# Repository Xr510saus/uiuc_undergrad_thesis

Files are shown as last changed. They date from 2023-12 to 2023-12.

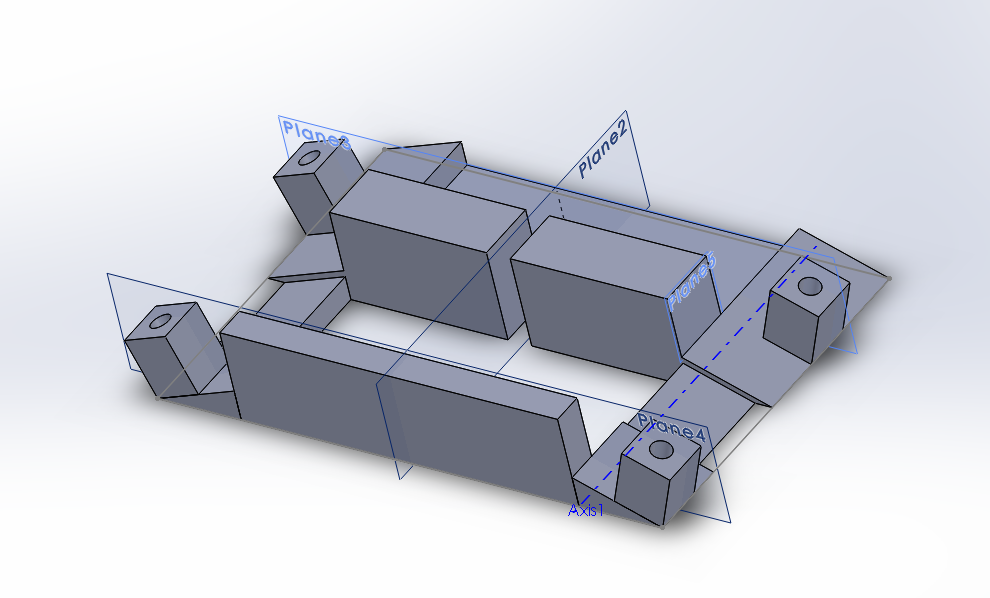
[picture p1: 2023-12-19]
images/chassis 2.png

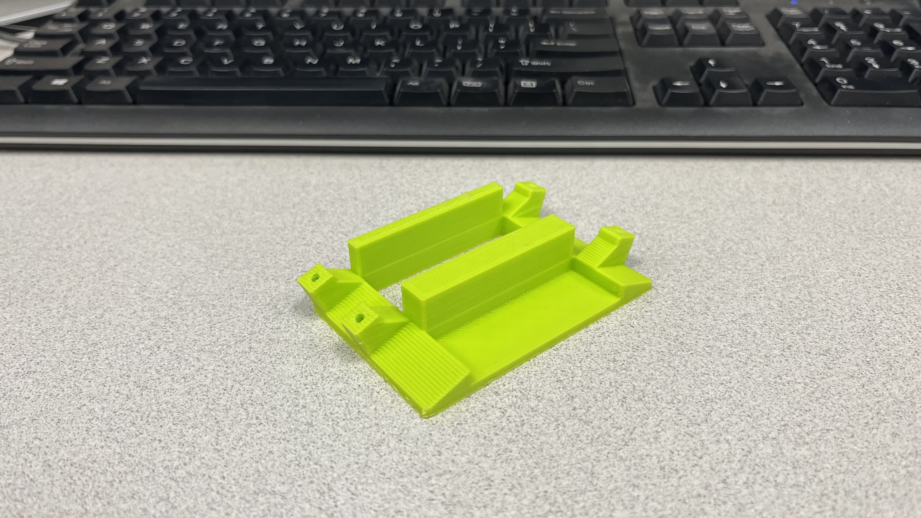
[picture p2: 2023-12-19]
images/first chassis part 2.jpg

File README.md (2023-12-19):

# uiuc_undergrad_thesis

## Project description

For my undergraduate (UIUC) thesis, I designed a cable-driven soft robot to crawl on 2D surfaces. This repo contains the entire history of the project, which lasted over my final two semesters at UIUC, starting from my funding application, through my progress reports, and finally ending at the FINAL DELIVERABLES directory, which contains my actual thesis and the slides I presented at the Undergraduate Thesis Symposium.

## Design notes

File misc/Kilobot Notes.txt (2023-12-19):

Purpose of swarm robotics:
* Validate collective control algorithms irl, not just through simulation

What other groups have done:
* Tested out on 10s, 100s of robots
* Limited by robot cost and operational complexity
	* Turning robots on/off, charging, controlling, and programming

Main point:
* All operations of the robot must work on the collective as a whole and be scalable

Kilobot:
* $14 worth of parts
* 5 min assembly
* Features
	* Differential drive locomotion
	* On-board computation power
	* Neighbor-to-neighbor communication
	* Neighbor-to-neighbor distance sensing

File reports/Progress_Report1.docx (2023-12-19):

Stephen Zhu

Srzhu3

ECE 496

In the past few weeks, I created some actuators to determine what parameters I would be interested in testing. It was my first time making CAD files to create molds, so it took some time to model the actual actuators before creating the molds and printing them using our 3D printer. I made 4 different molds, switching between the height of the actuator (15mm and 30mm) and the canal width, defined as the width between the valley and the bottom of the actuator (2.5mm and 7.5mm). Another mold was made with actuator height 25mm and canal width 5mm, but with double the width of the actual actuator. Included are two images, the first one shows one side of the mold for the 15mm 2.5mm actuator, while the second shows one side of the mold for the 30mm 7.5mm actuator. From the images, the canal width can be seen as the distance from the top of the molds to the peaks of the triangles

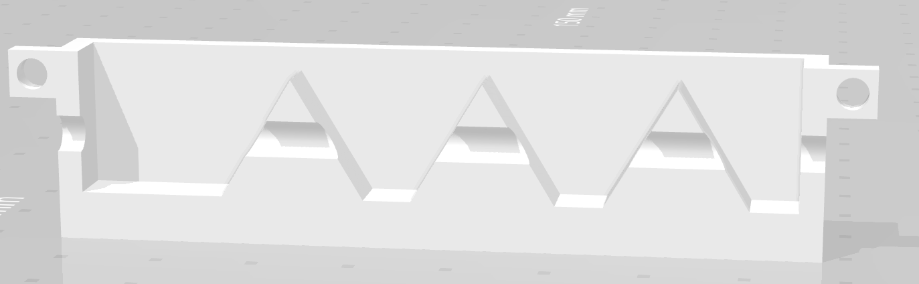
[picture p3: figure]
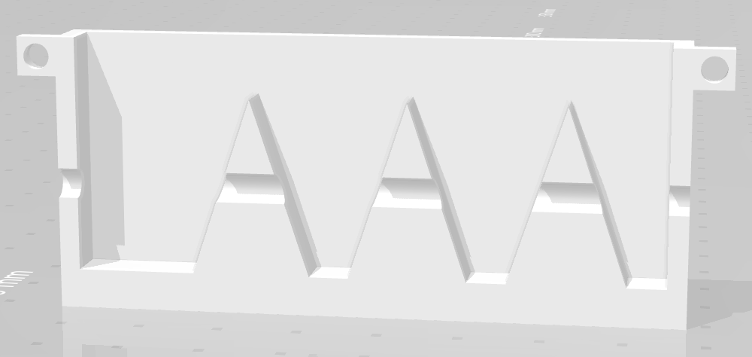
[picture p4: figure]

The molds were made such that each mold has two halves that can be connected by screws on both ends. In the middle, a cylindrical cavity is made, so that before each half is pushed together, a piece of tubing can be put inside the cavity. Silicon rubber is then poured into the mold and allowed to harden.

To further process each actuator, when the actuators are taken out, additional bits of rubber are trimmed off, and the parts of the tubing that aren’t within the actual actuator are cut off. Below are the two actuators made from the above molds

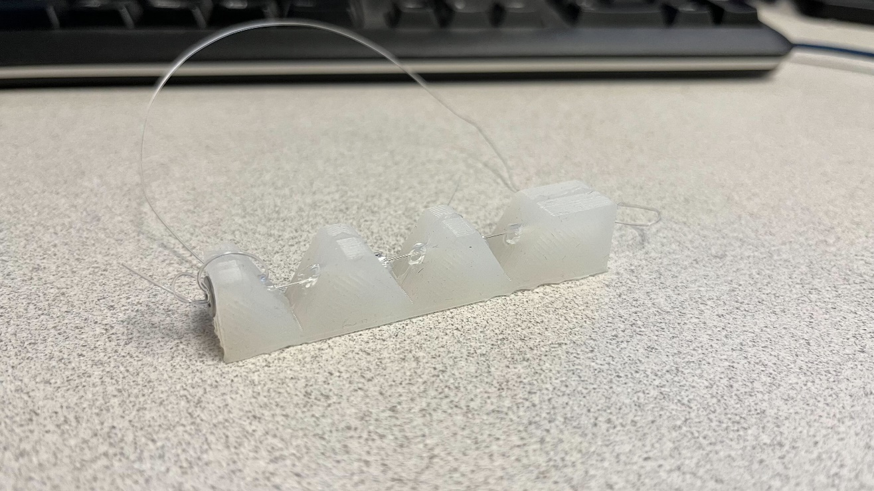
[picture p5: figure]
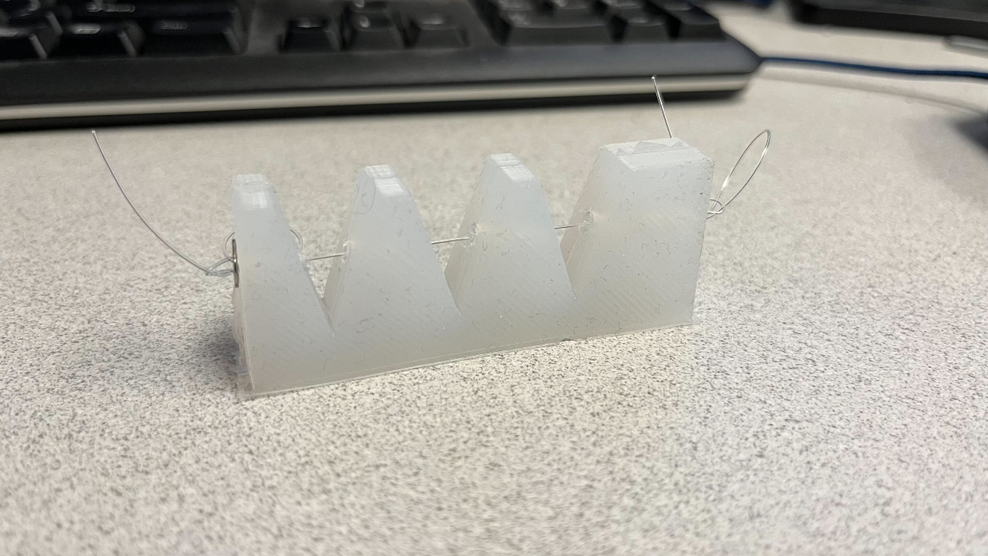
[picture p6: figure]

A total of 10 actuators were made, using two different materials (Ecoflex 50 and Dragon Skin 30) and each of the 5 molds. I then tried testing different aspects for each of the actuators and comparing them. Ultimately, the Ecoflex actuators were too soft to have any significant effect, and it only took at most 150 grams of weights to bend them fully. The Dragon Skin actuators were stiffer, and ranged from 110 g to 800 g of weight to bend fully. Below is a picture of the data taken, as well as a verbal description of the testing procedure to determine the weights needed to bend.

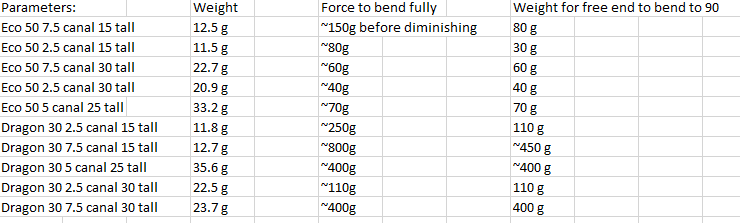
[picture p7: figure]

Testing Procedure:

1. Set actuator against side of table with vertical drop (ensure string doesn’t touch edge of table to factor out table friction
2. Add weights on to the hook weight and drop it onto the loop at the end of the actuator
3. Compare bend with bend through finger pulling
4. Change weights and redrop onto the line to ensure there isn’t any retention of shape from the actuator that affects the reading
5. Record amount of weight that is close enough to the full finger bend distance before significant diminishing marginal bend

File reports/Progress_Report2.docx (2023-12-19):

Stephen Zhu

Srzhu3

ECE 496

In order to test out the previously made actuators, I had to design a prototype body for the robot to attach the actuators to. Below is an image of the first design I made in SolidWorks. These designs were 3D printed, as we have not yet finalized the design for the robot itself, and 3D printing is significantly quicker and easier to make prototypes with.

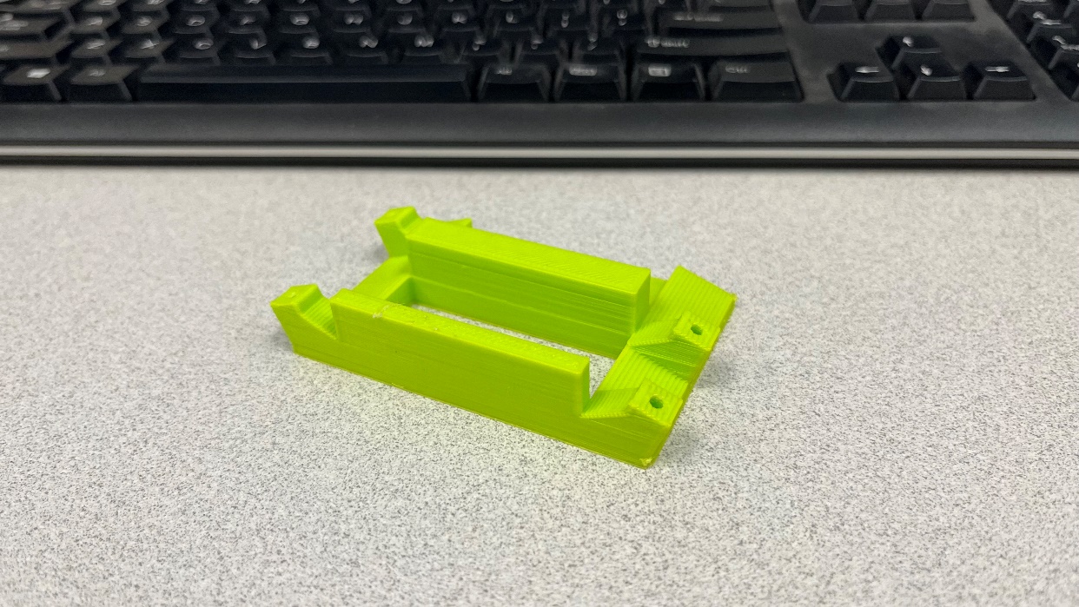
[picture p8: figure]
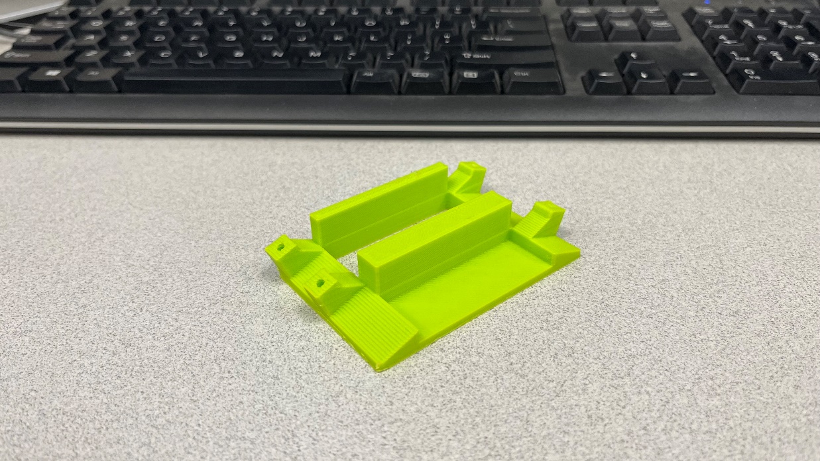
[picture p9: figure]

A few problems came with this design. First, the underside of the back half of the robot was too thick, so it added on a lot of time to the print. Second, I wanted to place a servo in the center to actuate the actuators on both sides, but my design failed to account for the fact that one end of the motor had cables exiting it, so the servo couldn’t fit inside the space I allotted it. Lastly, I designed the body in such a way that I could test the 15mm tall actuators on the “left” side and the 30mm tall actuators on the “right” side. This limited me from testing 30mm actuators on both sides, but since I had only 1 of each actuator, and I wanted to test the actuators first, this wasn’t a huge issue.

With the actual tests of the actuators, I quickly realized a trend. In the previous report, I included a table of how much weight it took to bend the actuators and one column detailed the weight needed to fully bend the actuator. Any actuator that had less than 400g as its entry wasn’t able to move the printed body at all. In other words, the Ecoflex 50 actuators were all too soft to have any noticeable effect on movement, and only a select few actuators were actually stiff enough to cause movement. It should be noted that the slopes that the actuators are attached on are at 20 degrees above the horizontal. When the actuators that were actually able to move the body were attached, some of them were stiff enough to raise the body above the ground.

The circuit to move the body was made using an ItsyBitsy 3V development board, attached to a computer though a USB micro cable. The reason it was attached to a computer was to ensure the voltage and current were high enough to run the servo. The program to actually move the servo was made on the Arduino IDE, as the ItsyBitsy board is capable of supporting Arduino IDE. Below is a picture of the circuit on a breadboard.

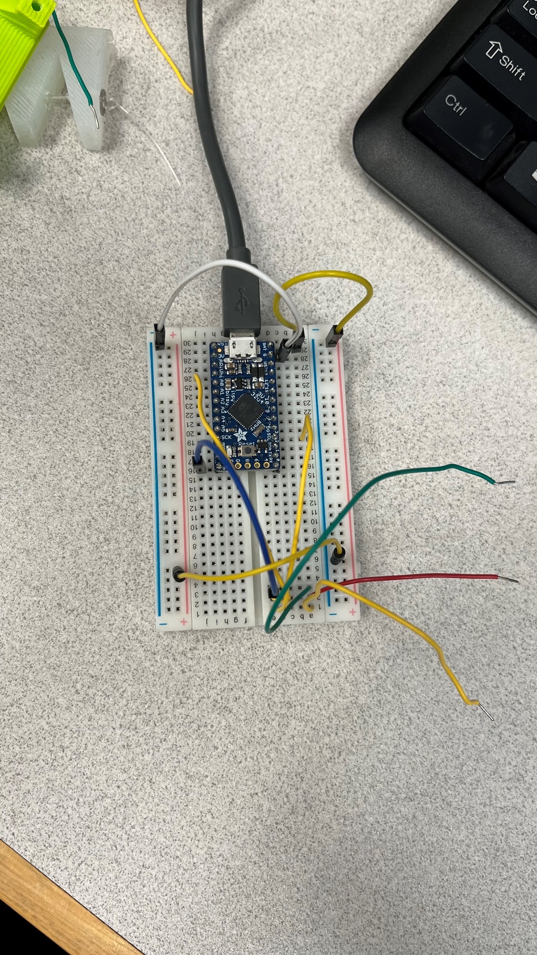
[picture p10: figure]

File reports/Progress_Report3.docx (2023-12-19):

Stephen Zhu

Srzhu3

ECE 496

To address the previous problems with the body, I redesigned it to allow space for the servo, reduce the print time, an allow the same actuator to be put on both sides.

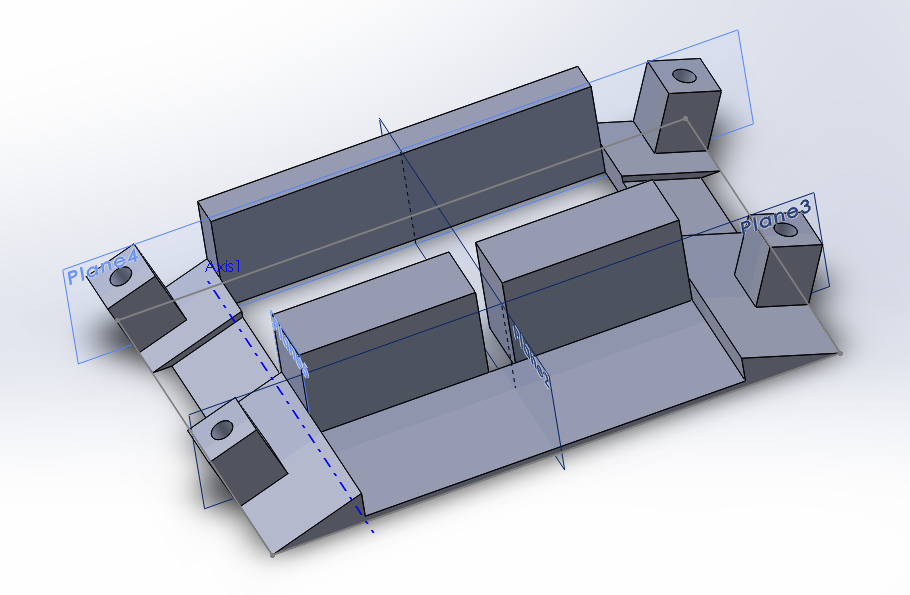
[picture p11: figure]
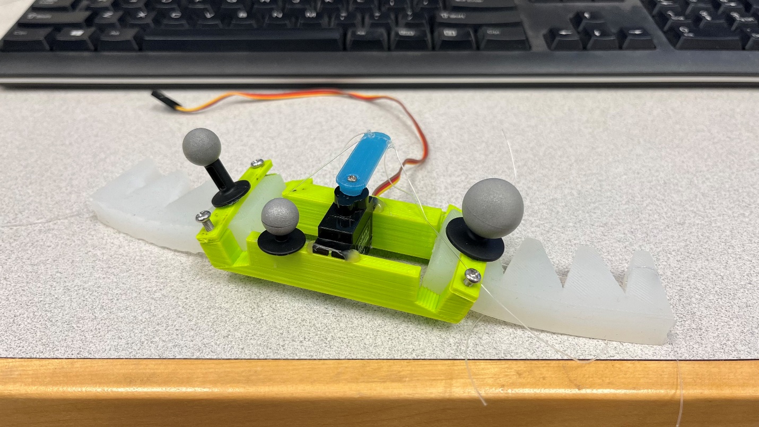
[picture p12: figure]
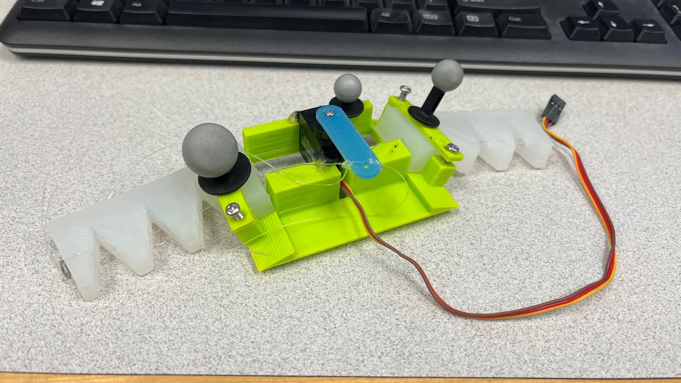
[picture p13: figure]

Additionally, grooves were introduced within the actuator attachment points to constrain the 15mm tall actuators so that they won’t wiggle around when put in. Additionally, the actuators that were able to move the body were duplicated (15 tall, 7.5 width canal and 30 tall, 7.5 width canal) and new actuators with 20 degree bends at the end were created.

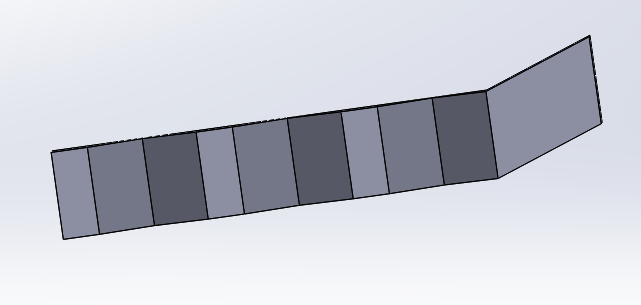
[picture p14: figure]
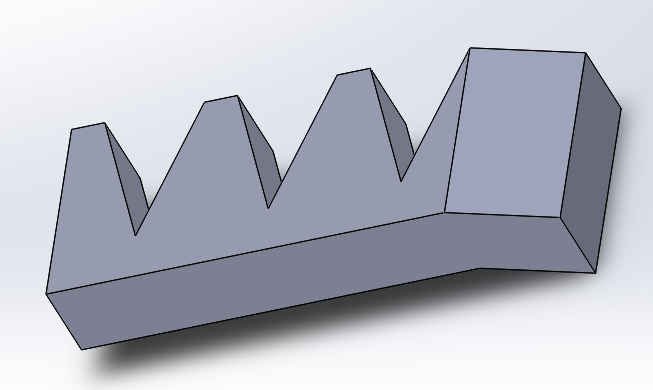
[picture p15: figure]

These actuators were made to account for the 20 degree slope that is on the body, and to bring more of the actuator to touch the ground. These were modified from the 30 tall, 7.5 width actuators. Each pair of the actuators were attached to the body and tested for speed (efficiency) though a motion capture system. Since the motion capture system is too far away for the cable to reach, the circuitry was modified to allow for 2 LiPo batteries in series to power the system. Below are graphs made using the data.

15 tall, 7.5 width; velocity: 0.8 mm/s

30 tall, 7.5 width; velocity: 2.1 mm/s

30 tall, 7.5 width, bent actuator; velocity: 0.3 mm/s

From the data, we can see that in terms of overall speed, the 30 tall, 7.5 width actuator performed the best. Additionally, I now believe that what caused the body of the robot to move is due to the edges of the actuators, not the bottom face, which explains why the bent actuators performed worse. It should be noted that the 15 tall, 7.5 actuator was so stiff that the body was completely off the ground, and when the actuators began moving, the robot tipped over slightly due to how unbalanced the system was.

In the future, I want to design some actuators with grooves at the bottom, and see if that can artificially create an “edge” for the actuators to move off of. Additionally, I want to experiment with making actuators with “legs bent in one direction,” which would allow the actuator to return smoothly to its default position, but give a lot of resistance when the actuator is being pulled.

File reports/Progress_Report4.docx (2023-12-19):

Stephen Zhu

Srzhu3

ECE 499

Progress Report 4

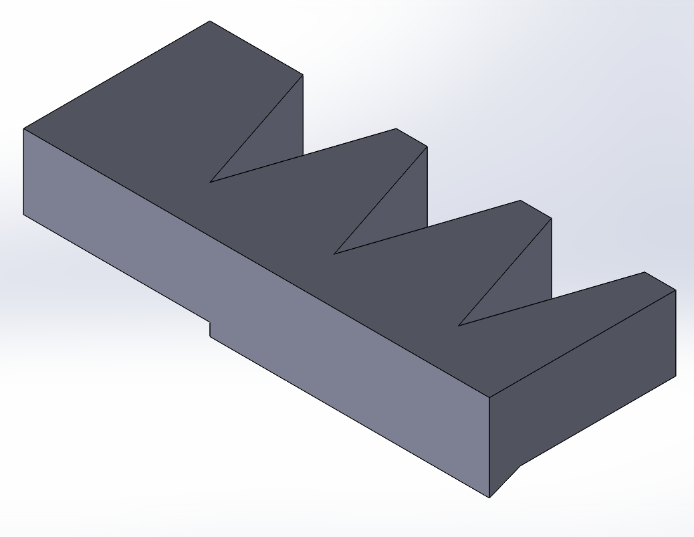
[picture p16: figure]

I continued to test out different actuator designs, expanding on the thought of introducing “legs” or other shapes on the bottom of the actuators. My main focus was on improving the “edge” of the actuator, since the net motion of the robot seemed to be driven by how well the edge was able to push off against the ground. As shown in the images below, I tried designs such as adding a more distinct “edge” to the actuator and three “legs” to the edge.

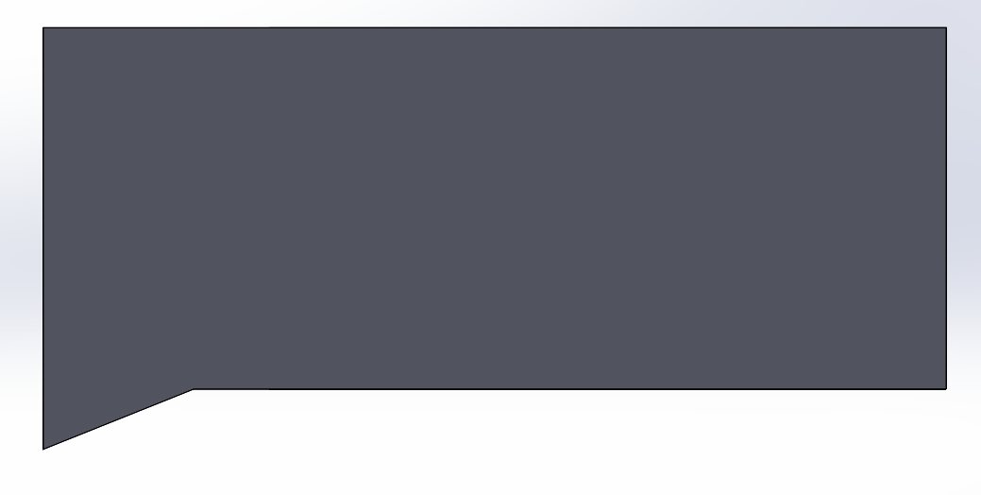
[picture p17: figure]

Single-edge isometric view Single-edge side view

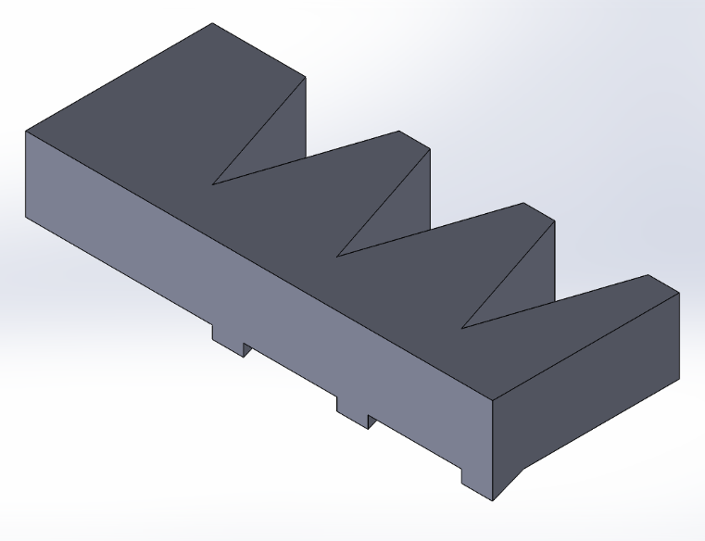
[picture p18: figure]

Tri-edge (tri-leg) isometric view

Additionally, I experimented with adding a tilt into the actuator, to see if that would enable better “grip” from the new edges, as well as reversing the direction of the legs to see if that would enable movement in the reverse direction.

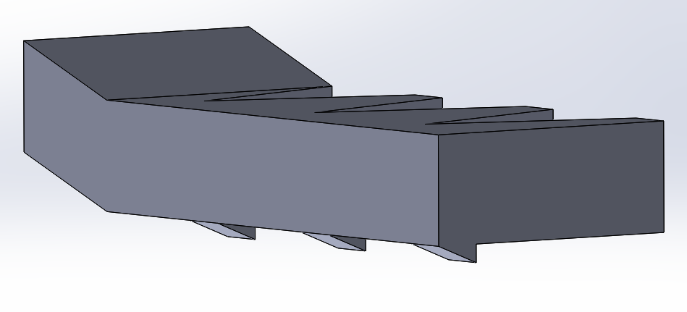
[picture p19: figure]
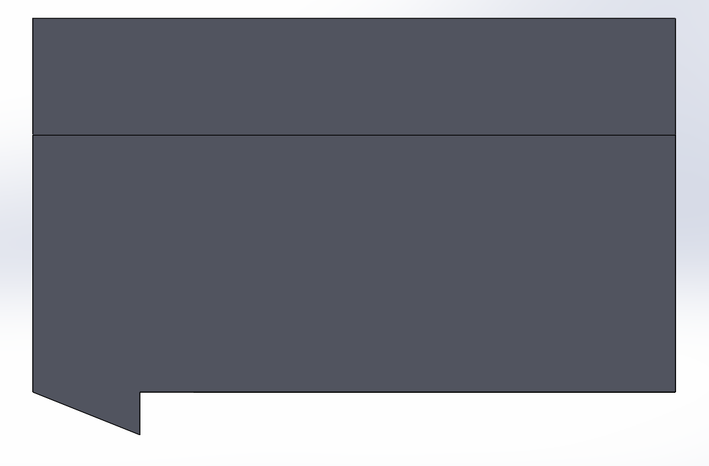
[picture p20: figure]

Tilted and reverse-leg isometric view Tilted and reverse-leg side view

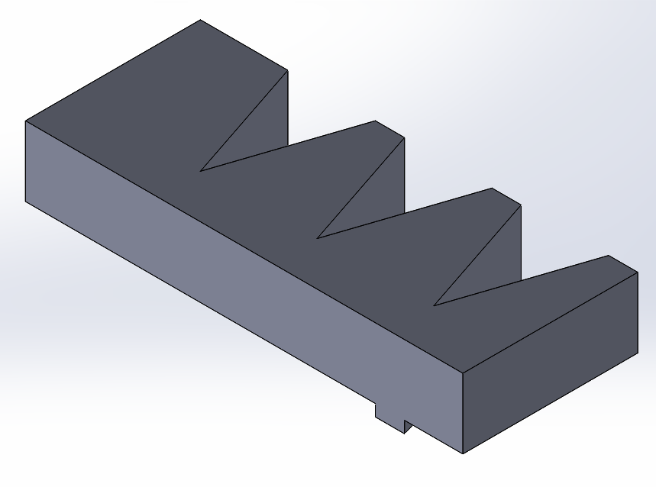
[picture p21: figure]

After using the motion capture system to test the efficiency of the actuators, it was clear that introducing a tilt to the actuator was detrimental to its efficiency, since there was less pressure pushing the edge of the actuator into the ground. Reversing the legs also did nothing. Between the single-edge and tri-edge designs, the tri-edge performed better. On further inspection through video footage, it seemed like when the actuators were being pulled, the smooth side of the legs would get pulled back normally. However, when the actuator was being released, the edges of the legs would catch the ground, causing them to greatly increase the friction and create a larger net motion than the other designs. I then tried to create a design with only one leg to further reduce the friction when the actuator was being pulled, but it proved to be less effective than the design with three legs.

Single-leg design

Lastly, I experimented with increasing the speed of the servos. As expected, the faster the servos went, the faster the robot would go through an entire movement cycle, and thus the faster the robot moved.

Below is the graph of the increased speed, tri-edge/leg design.

From the line of best fit, the velocity of the robot was around 9.1 mm/s.

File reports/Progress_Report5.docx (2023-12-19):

Stephen Zhu

Srzhu3

Progress Report 5

With the actuator design finalized, I turned to working on designing the circuitry on Eagle and making the soft prototype body.

For the circuitry, I used the Adafruit ItsyBitsy board and Arduino to control two servos, one for each actuator. The initial prototype relied on one servo to pull each actuator back and forth, but with the use of two servos, separate control of each actuator can be achieved. I then experimented with using a 3V-5V voltage booster, since the nominal voltage of the battery was on the low side for the servos. I eventually found that just directly linking the servos to the output of the booster without extra resistance was fine and didn’t damage the servos, and I finalized the circuit design, shown below. The rightmost component is the ItsyBitsy board, the top left is the battery-to-board connector, the middle left is the 3V-5V booster, and the bottom two are the servo-to-board connectors.

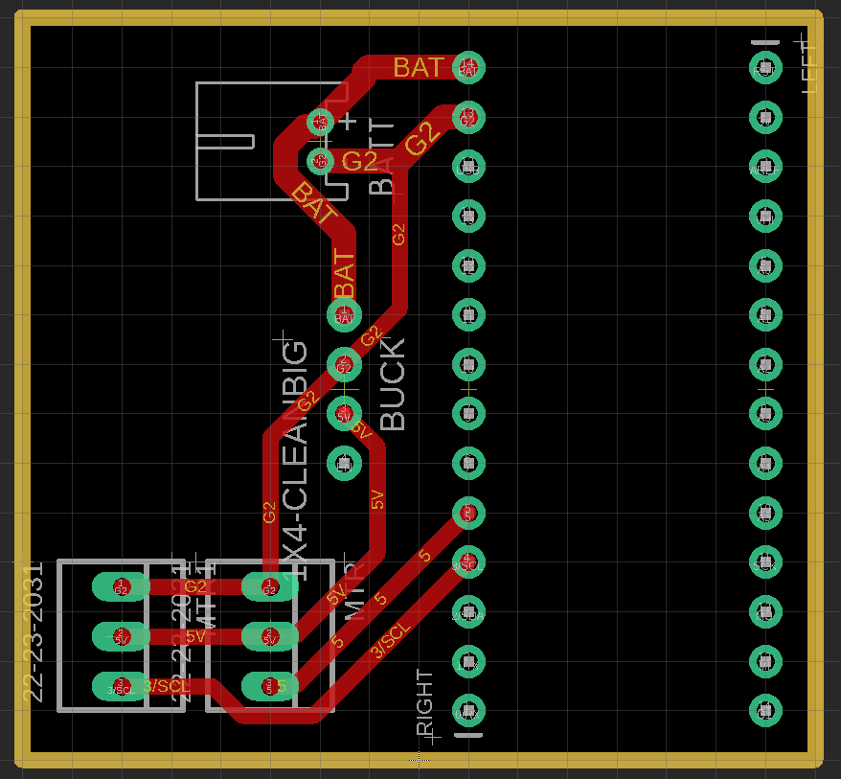
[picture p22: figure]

I then began to prototype a soft body, to verify if my prior experiments would work once I shifted away from the 3D-printed body. Initially, I tried making a mold based off of the previous design, but the screw clamps I used to hold the actuators in place wouldn’t work on a soft body. Also, the lack of material surrounding the servos proved to be detrimental, since the servos would turn in place rather than pull on the actuators’ cables.

To fix this, I surrounded the servos with material, and adjusted the actuator housing so that I would need to use more silicone rubber to glue the actuator to the body. Additional, I added a small compartment to hold the battery, and created a well to be able to glue the circuit board onto the body better. The design is shown below.

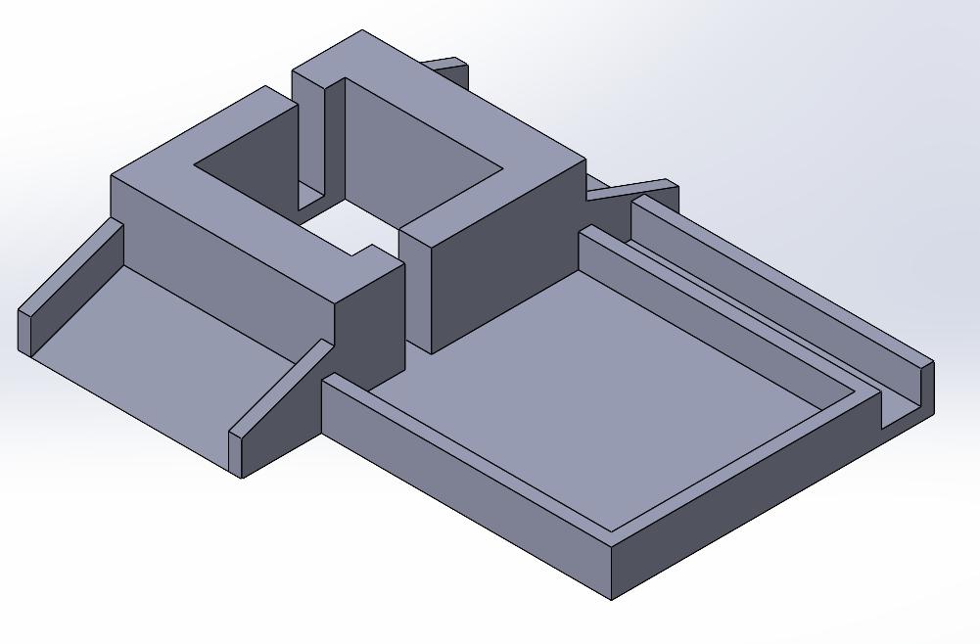
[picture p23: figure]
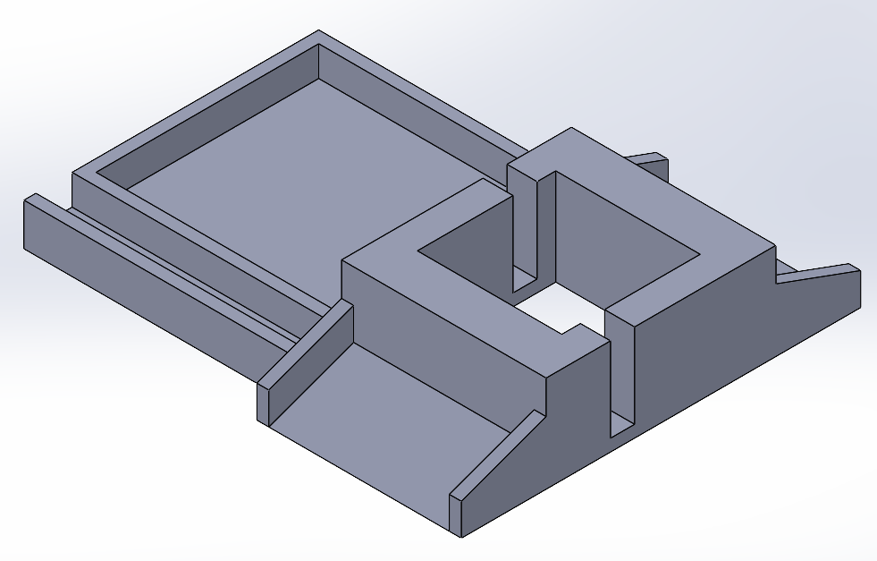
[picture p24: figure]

With these two elements, we were finally able to make the robot completely untethered and gather data on it using the motion capture system. The completed prototype is shown below, as well as the data.

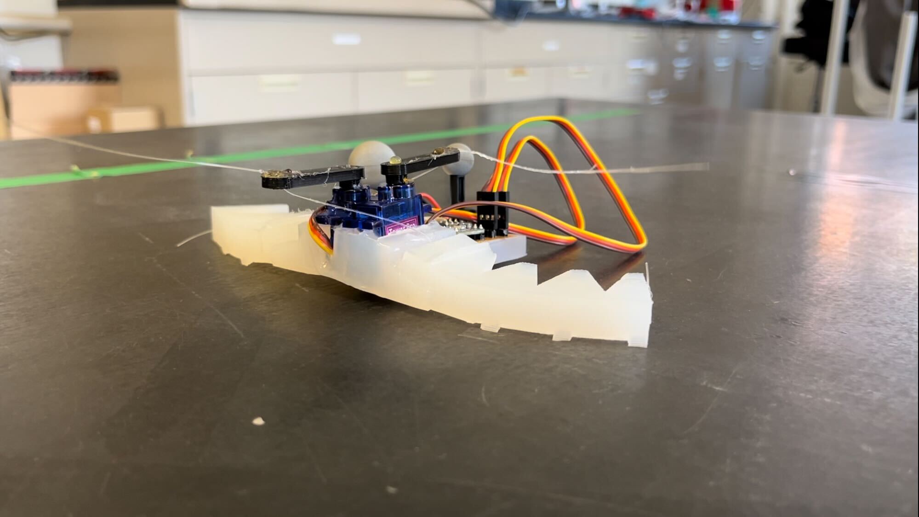
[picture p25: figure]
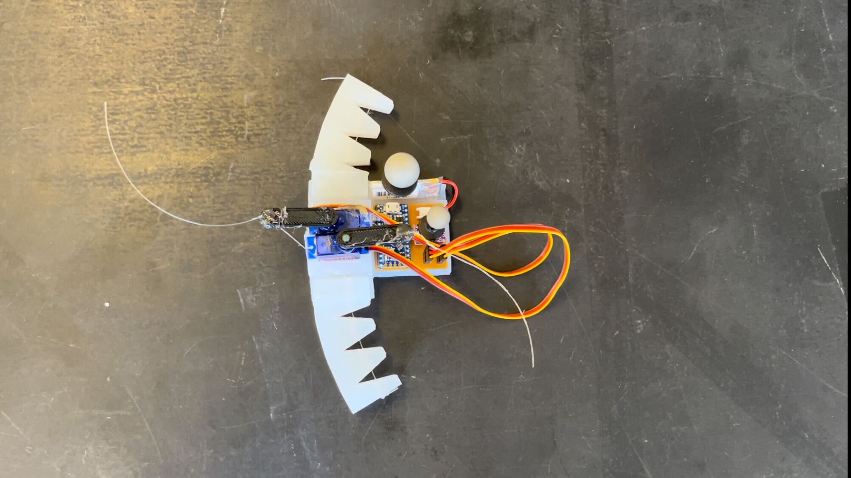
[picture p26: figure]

From the data, the net velocity is around 4 mm/s this is a slight decrease in the previous results, though there are several factors that influence this. As expected, having a soft body produces more friction overall in comparison to a 3D printed body, so the performance decreases. Also, the servos used for the soft body were less powerful than the one used in the printed body prototype, so the speed of the servos had to be decreased. Lastly, due to the soft body, the body itself bends a little bit, which in turn bends the actuators less. Thus, there is less pressure against the legs of the actuator, which causes less directional force to be generated.

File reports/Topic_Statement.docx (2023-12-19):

Stephen Zhu

Srzhu3

ECE 496

Soft robots are robots built with compliant materials. In practice, this has several advantages over traditional robotics, namely in terms of adaptability, safety, and cost. Professor Yang Zhang, who was at UIUC but recently moved to the University of Michigan, research group has developed an open-source finite element platform for the modeling of soft robots. This platform, Kraken, is being used to model the contact mechanics, statics, and dynamics of soft robots. Recording high-quality experimental results with more complex soft robots are required to further assess and improve the performance of Kraken.

Currently, the soft robots available to Professor Zhang's group are limited to planar motion or operate only in highly controlled environments, with one end of the robot being fixed. My role in this project will be to help design and fabricate novel soft robot designs that can operate in 3 dimensions and are capable of large-scale locomotion. I will spend the first semester designing the soft actuators and control circuitry and the second semester assembling various configurations of the system and developing feedback controllers.

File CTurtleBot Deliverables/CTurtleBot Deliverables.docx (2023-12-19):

# BOM (per robot)

2x Servo (https://www.digikey.com/en/products/detail/adafruit-industries-llc/169/5154651) ($5.95 each)

1x 3V-5V Booster (https://www.digikey.com/en/products/detail/adafruit-industries-llc/4654/12697636) ($3.95 each)

1x 2-pin JST Connector (https://www.digikey.com/en/products/detail/jst-sales-america-inc/S2B-PH-K-S-LF-SN/926626) (<= $0.17 each)

1x ItsyBitsy 3V Dev Board (https://www.digikey.com/en/products/detail/adafruit-industries-llc/3675/8031669) ($11.44 each)

1x 3V LiPo Battery (https://hobbyking.com/en_us/turnigy-200mah-1s-20c-lipo-pack.html) ($3.49 each)

1x Set of Dragon Skin 30 (https://shop.smooth-on.com/dragon-skin-30) ($36.89 each) (each robot uses around 100 g total)

2x Washers

1x Spool of Fishing Line (or fishing line in general)
2x 3-pin board connector (can be used from extra connectors that come with the ItsyBitsy or booster)

Total price (of linked parts): $67.84

- Assuming each set of Dragon Skin 30 comes with 900 g total, using only 100 g would bring the price down to $34.95

# Body Structure Files

- ALL FILES Printed with High Speed PLA profile
- Prototype Files (https://drive.google.com/file/d/1b_J-L70NpBMhjSTjukNvuKA0TYcu7FGA/view?usp=sharing)
- Final Soft Body Files (https://drive.google.com/file/d/1pev9rPWN_qg7TgqdF9Gr0Ul88zvJY38Y/view?usp=sharing)

# Electrical Schematic and Board Files

- Milled with one-sided copper sheets, copper side face up in mill
- 1/64” drill bit
- Electrical Files (https://drive.google.com/file/d/14HYk3L7_f8Piv6ouqpcXZL93k8bdjsIz/view?usp=sharing)

# Software Files

- USB-A to Micro USB cable needed to flash code onto board
- Programmed through Arduino IDE
- Program Files (https://drive.google.com/file/d/1dbuXq2EUp_y6uo9tRPLNIkV_PR0MaL2D/view?usp=sharing)

# Build Instructions

## Actuators

1. (OPTIONAL) If different shaped actuators are desired:
  a. Open the actuator_mold_construction folder within the body_files folder
  b. Adjust the actuators within easymodactuator_grove* files
  c. Open up the flatgroove* files and rebuild each one
  d. Open up the grooveblock* files and edit the Split features
  e. Under the Resulting Bodies section, for each body double-click on <None> (if there is already a title, double-click the title name instead), New Part, Browse, and enter in whatever name you desire, in the directory you want to save the file to.
  f. Click on the green checkmark to finalize the split; each part of the mold should be autogenerated and appear as separate SLDPRTs
2. Save each mold SLDPRT part as a STL file, and print them using a 3D printer
3. For each mold pair, put a piece of tubing in the cavity formed when pressing the two pieces together
4. Use two screws to screw together the mold parts and tape on the bottom half of the mold to prevent as much material from leaking out as possible
5. Mix together 15 g of EACH part of Dragon Skin 30, and use the vacuum chamber to remove as many air bubbles as possible
6. Pour in the material to the molds, and wait at least 4 hours for the actuators to cure
7. Take the actuators out of the molds
8. Use scissors to cut the exposed tubing, until the tubing is flush against every surface
9. For the surface of the actuator that formed as the “top” of the actuator in the mold, put that surface face down on a table and use an exacto-knife or similar tool to precisely remove excess material
10. Any other stray tags/bits of material may be picked off by hand
11. Feed fishing line through the tubing and put a washer on the non-base end of the line.
12. Secure the fishing line to the non-base end by tying a knot

## Soft Body

1. (OPTIONAL) If a different body shape is desired:
  a. Open the soft_body_construction folder within the body_files folder
  b. Open the chassis.SLDPRT file and adjust as necessary
  c. Open the cassem assembly file and rebuild
2. Open the cblock.SLDPRT file and save as a STL file
3. Print out the STL file using a 3D printer
4. Mix together 20 g of EACH part of Dragon Skin 30 and use the vacuum chamber to remove as many air bubbles as possible
5. Pour the material into the molds, and wait at least 4 hours for the material to cure
6. Take the soft body out of the mold; be careful as some parts are easier to tear than others
7. Use an exacto-knife or other similar tool to remove excess material in undesired places

## Circuitry

1. Locate the turtlebot.brd file within the electrical files
2. Use double-sided tape to secure the one-sided copper sheet to the mill bed
3. Use 1/64” drill bit
4. Print out the board
5. Solder the components to their respective spots
6. Attach the servos to the 3-pin connectors
7. Upload the code onto the dev board
8. Place the PCB into the designated slot on the soft body
9. Place the battery into the designated slot on the soft body
10. Use extra Dragon Skin 30 to pour into the slots, to “glue” the places on the board


## Last Steps

1. Use extra Dragon Skin 30 to glue the actuators to their designated slots; make sure to have the actuators flush against the slope on the soft body (unless the design was changed)
2. Use extra Dragon Skin 30 to glue the servos in place
3. Attach the servo attachments (print them out first) to the servo heads and secure with hot glue
4. Feed the fishing lines through their respective servo attachments and secure each line with hot glue
5. The robot will begin moving once the battery is connected to the board

# Future Steps

- Add wireless control
- Flip side to put actuators on to see if the robot can “pull” itself instead of push
- Change design so that the sloped area to attach the actuators to is flat, and the actuator has a bend in it
  - Potentially makes gluing the actuator on much easier
- Design better method to attach actuator to soft body
- Further improve actuator design to achieve faster speed
- Find better servos that can handle faster turning speeds
- Adjust battery slot so that it doesn’t block the USB port on the dev board, but can still reach the battery connector
  - Maybe redesign the board if it makes it easier to do so

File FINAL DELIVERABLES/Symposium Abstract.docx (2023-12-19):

CTurtleBot – A Turtle Inspired Soft-Robot

Stephen Richard Zhu

The Department of Electrical and Computer Engineering

Spring 2023

Advisor: Professor Yang Zhang

ABSTRACT

The goal of this project is to design and prototype an untethered soft-robot, capable of traversing across 2D surfaces, as a test bed for hysteresis-based control systems. To achieve this, we chose cable-driven, silicone rubber actuators as the primary method of movement, due to their compliant and elastic nature. In addition, we created and 3D-printed a prototype chassis as an intermediate for testing the actuators. Lastly, we designed a custom PCB to control the actuators and enable an untethered design.

Since silicone rubber has a high coefficient of friction, the biggest challenge of this project is overcoming the friction of the actuators in only one direction to create a net motion. To overcome this, we first tested different types of rubbers of varying stiffness to determine a balance between the force required to actuate the actuators and the capability of the actuator to move the robot with its elasticity. After choosing a material to work with, we experimented with having the actuators flat on the ground versus approaching the ground at an angle, introducing curvature into the actuator. Analyzing the results through motion capture and videos, we found that the “curved” actuators created more net movement, since the edge of the actuator caught and pushed off of the ground more compared to the flat actuator. Finally, we added different shapes to the edge of the actuators to see if we could further improve performance.


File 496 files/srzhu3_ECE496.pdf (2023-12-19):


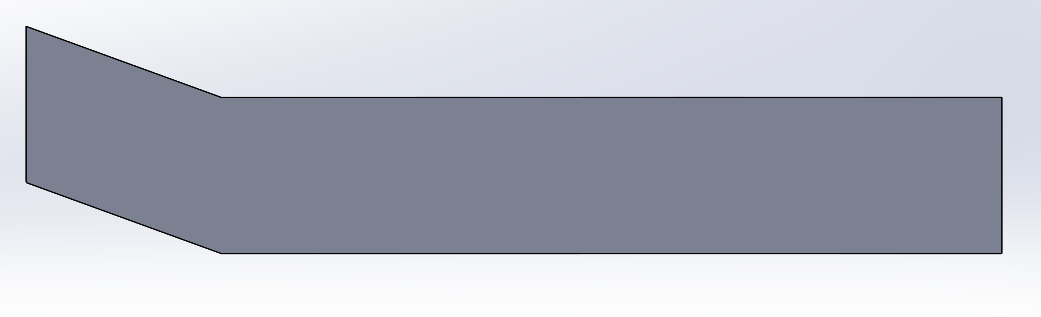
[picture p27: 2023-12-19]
images/bent side.png

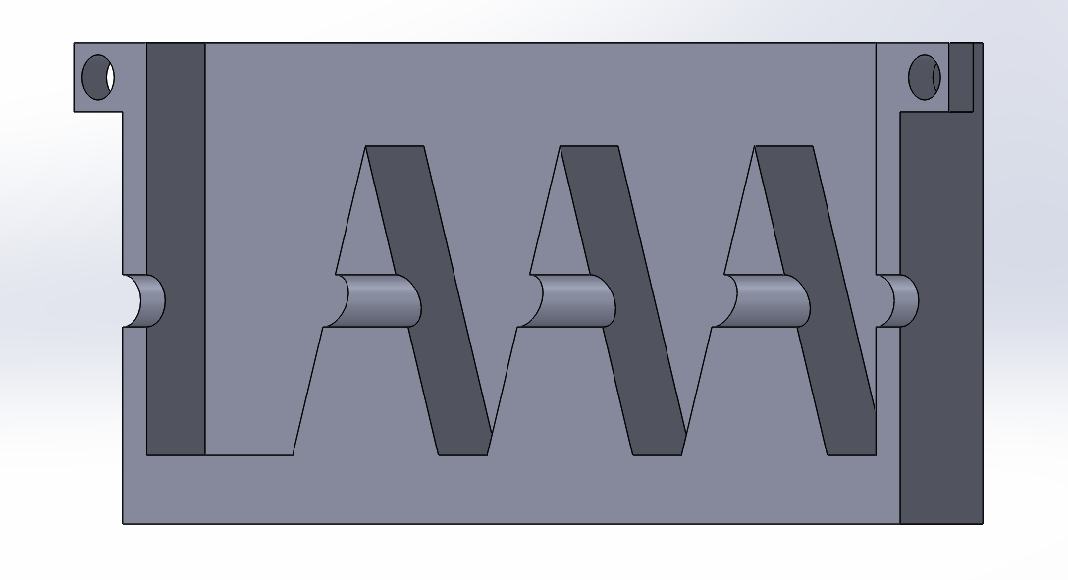
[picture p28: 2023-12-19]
images/actuator mold 45.png

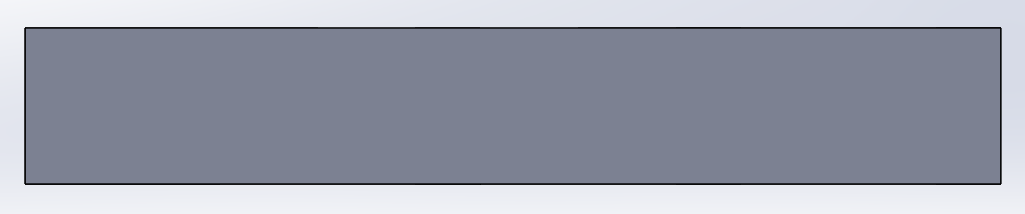
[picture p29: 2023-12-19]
images/norm side.png

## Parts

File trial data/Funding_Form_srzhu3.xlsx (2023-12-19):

Department of Electrical & Computer Engineering
University of Illinois at Urbana-Champaign
306 North Wright Street - Urbana, IL 61801
Ph: 217.333.8060
P U R C H A S E R E Q U I S I T I O N
Date: 12/02/2022 |  |  |  | Req. No.
VENDOR NAME |  |  | VENDOR - ADDRESS - CITY, STATE, ZIP, PHONE, AND FAX #, Email, Website
Digikey, HobbyKing, Smooth-On |  |  | https://www.digikey.com/
 |  |  | https://hobbyking.com/en_us
 |  |  | https://shop.smooth-on.com/
Requester: Name, netID & phone# |  | Stephen Richard Zhu, srzhu3, 8185716885 |  | For items costing $500 or more, indicate expected useful life of item:_______
ECEB Room Number & Attention of: |  | Talbot Laboratory 220C
Ship to: |  | University of Illinois - 104 South Wright Street, 100 Talbot Lab - Urbana, IL 61801
Required Delivery Date:
Comments: ENTER QUOTE # ( ALWAYS ATTACH A QUOTE IF VENDOR PROVIDES) |  | Items #1-6 are from Digikey, Item #7 is from HobbyKing, Item #8 is from Smooth-On (can also be bought from Eager Polymers, Reynolds Advanced Materials, or Techno Industrial Products [listed here: https://www.smooth-on.com/distributor-regions/usa/]).
Line Item | Quantity | Part / Catalog Number | Description | UNIT: Each/Case/gallon | Price per unit | Sub-Totals
1 | 5 | 1528-1076-ND | SERVOMOTOR RC 5V TOWERPRO | Each | 5.95 | $29.75
2 | 5 | 1528-4654-ND | MINIBOOST 5V @ 1A - TPS61023 | Each | 3.95 | $19.75
3 | 5 | 751-1227-ND | SENSOR REMOTE REC 38.0KHZ 45M | Each | 1.23 | $6.15
4 | 10 | 455-1719-ND | CONN HEADER R/A 2POS 2MM | Each | 0.17 | $1.70
5 | 5 | 1528-2500-ND | ITSY BITSY 32U4 3V 8MHZ EVAL BRD | Each | 11.44 | $57.20
6 | 5 | 1528-1374-ND | METRO MINI ATMEGA328/CP2104 | Each | 14.50 | $72.50
7 | 5 | 9067000498-0 | Turnigy 200mAh 1S 20C LiPo Pack | Each | 3.49 | $17.45
8 | 2 | Dragon Skin 30 | Dragon Skin 30 | Trial Unit | 36.89 | $73.78
TOTAL |  |  |  |  |  | $278.28
Charge To:
Chart-Fund-Org-Program-Activity |  |  |  |  | Items or
1-xxxxxx-933xxx-xxxxxx-xxxxxx |  |  | Account Title |  | % of total | Subtotal
1 |  |  | INDEPENDENT STUDY FUND |  |  | $0.00
2 |  |  |  |  |  | $0.00
3 |  |  |  |  |  | $0.00
4 |  |  |  |  |  | $0.00
 |  |  |  |  | TOTAL | $0.00
REQUESTED BY: SIGN AND PRINT NAME |  | Stephen Richard Zhu
APPROVED BY: SIGN AND PRINT NAME
Does this request include purchase of a class 3b or 4 laser? [ ] yes [x] no |  |  |  | Link to DRS Forms (http://www.drs.illinois.edu/rss/lasers/)
If yes, registration with the University Division of Research Safety is required.

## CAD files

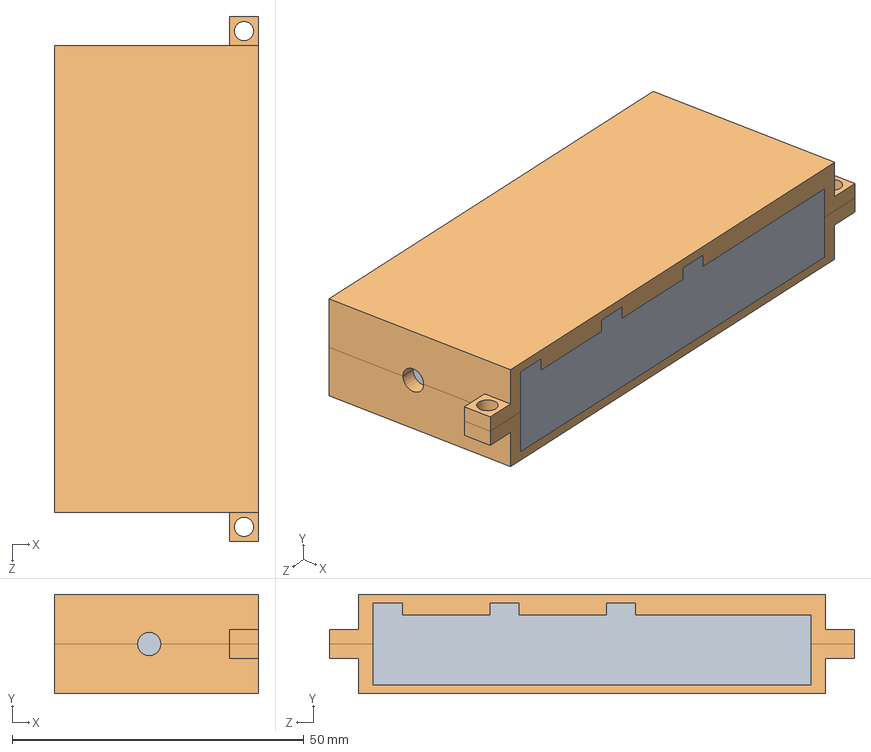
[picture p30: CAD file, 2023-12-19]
body_files/actuator_mold_construction/flatgroove.SLDASM
35.0 x 17.0 x 90.0 mm
easymodactuator_groove
grooveblock

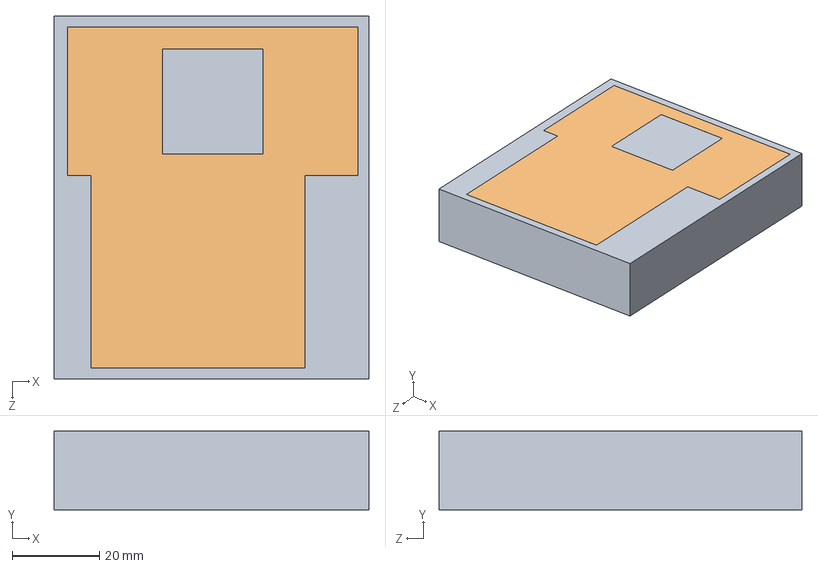
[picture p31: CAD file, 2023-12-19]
sw/soft mold/cassem.SLDASM
72.0 x 18.0 x 83.0 mm
cblock
chassis

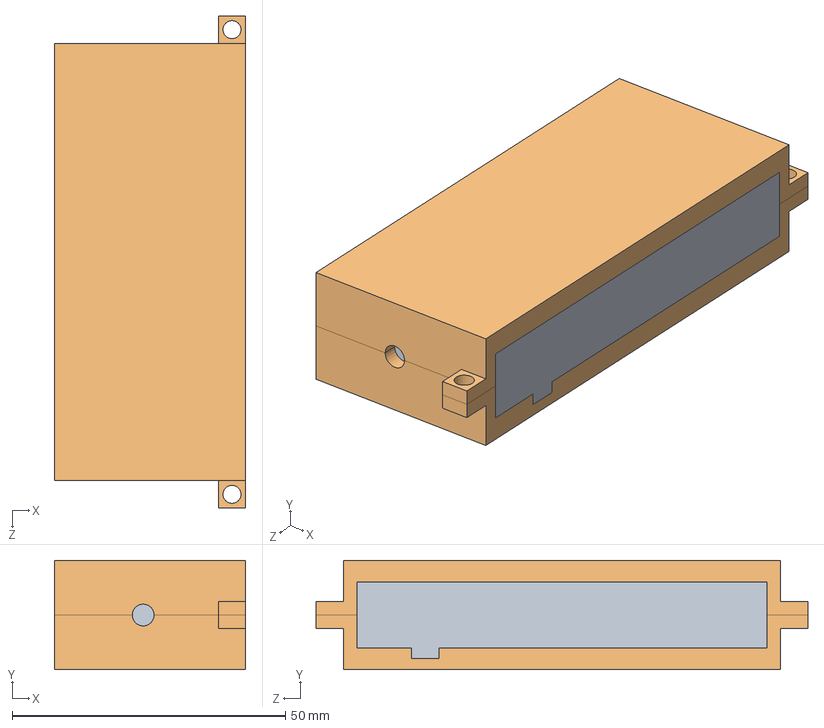
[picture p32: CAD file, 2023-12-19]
sw/last/sg_rev_assem.SLDASM
35.0 x 20.0 x 90.0 mm
sg_rev
sg_block_rev

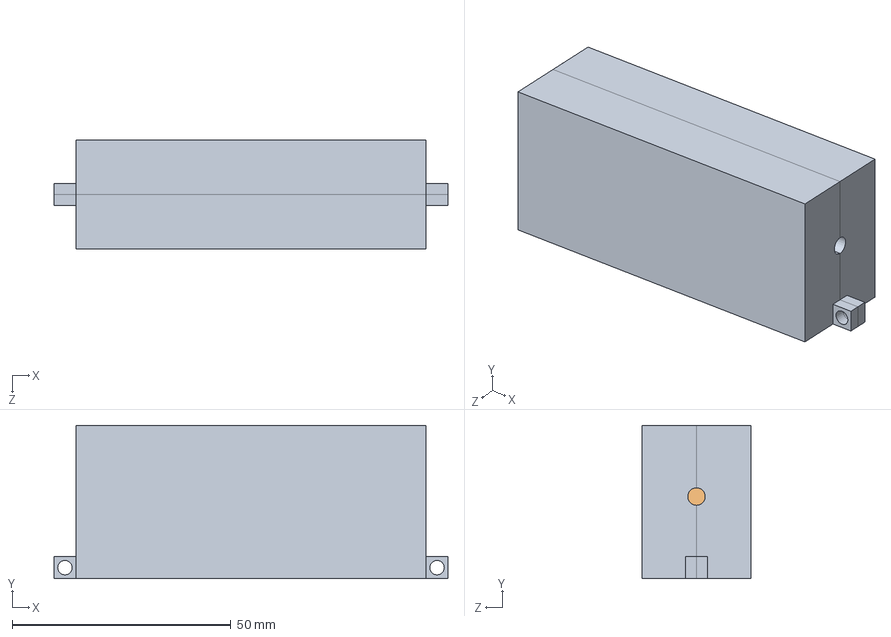
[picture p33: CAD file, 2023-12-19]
sw/tiltgroove_rev.SLDASM
90.0 x 35.0 x 25.0 mm
tiltgrooveblock_rev
easymodactuator_tilt_groove_rev

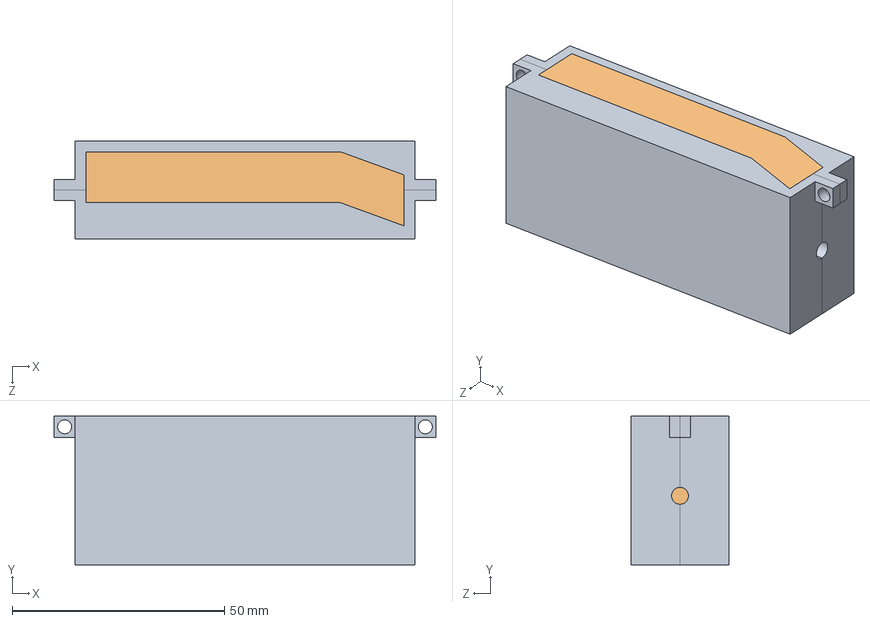
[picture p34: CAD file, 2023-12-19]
sw/tiltblock.SLDASM
90.0 x 35.0 x 23.0 mm
tiltblock
easymodactuator_tilt

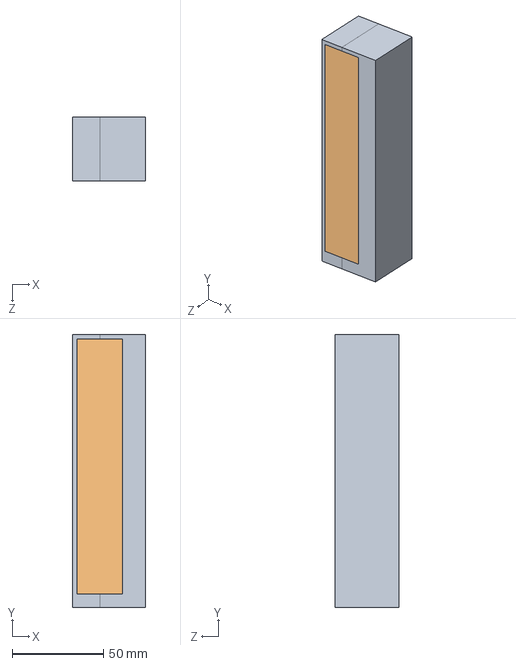
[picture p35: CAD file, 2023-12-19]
sw/Assem1.SLDASM
40.0 x 150.0 x 35.0 mm
blokc
easymodactuator

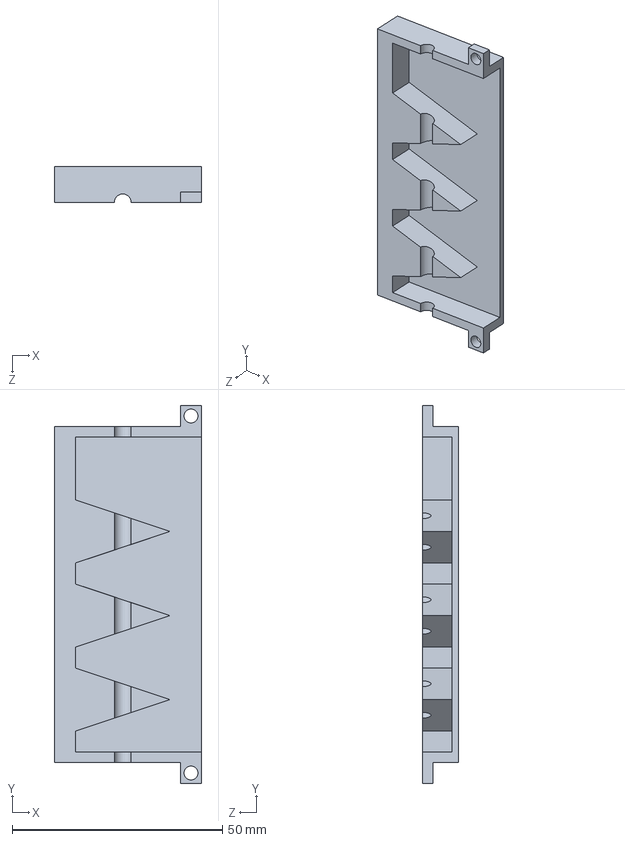
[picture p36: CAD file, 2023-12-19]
body_files/left_actuator_left.SLDPRT
35.0 x 90.0 x 8.50 mm

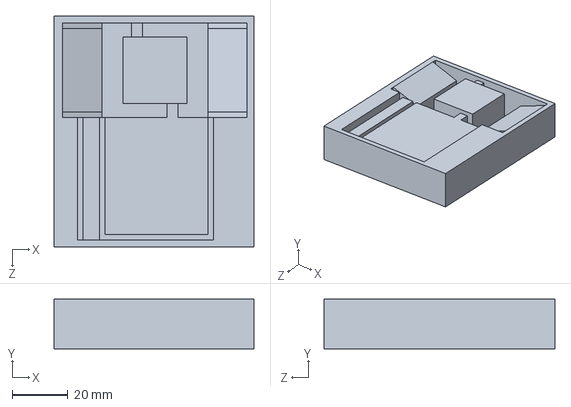
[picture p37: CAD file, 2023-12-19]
body_files/soft_body_construction/cblock.SLDPRT
72.0 x 18.0 x 83.0 mm

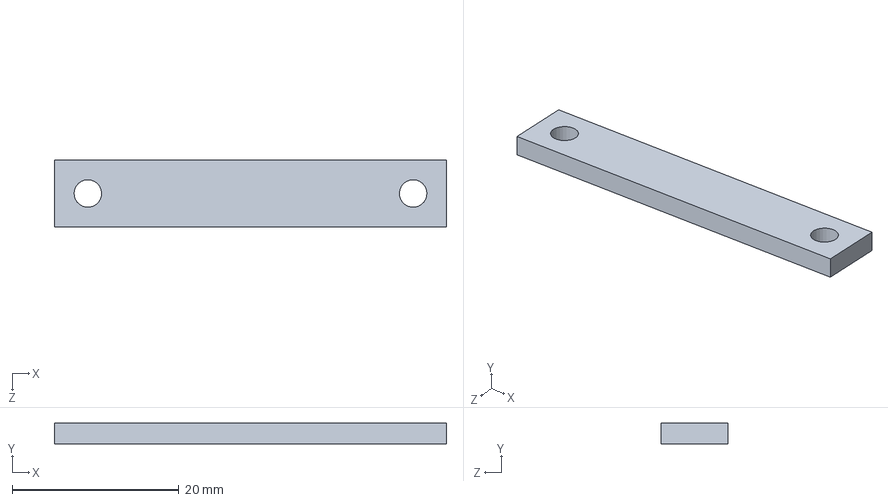
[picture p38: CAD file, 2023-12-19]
prototype_files/actuator_clamps.SLDPRT
47.0 x 2.50 x 8.00 mm

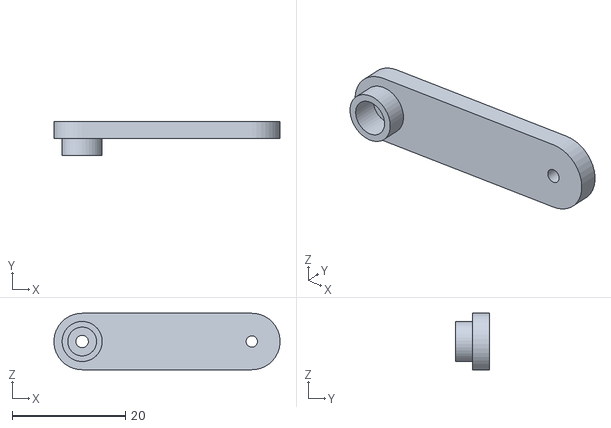
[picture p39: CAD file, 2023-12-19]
sw/arm/arm5.1.STL
40.0 x 6.00 x 10.0

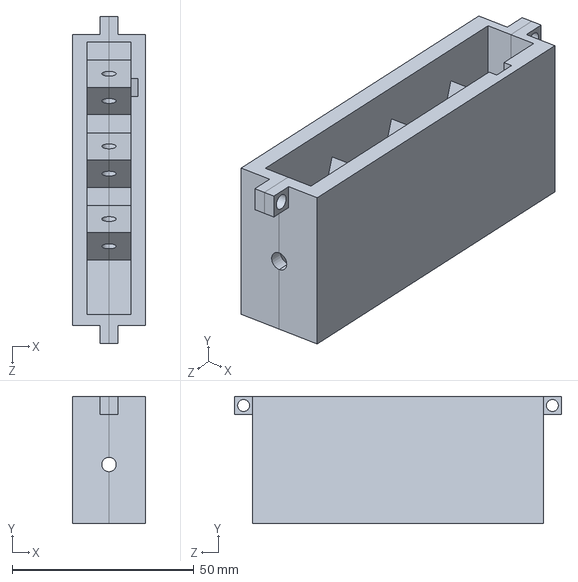
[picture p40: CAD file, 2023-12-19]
sw/last/sg_block.SLDPRT
20.0 x 35.0 x 90.0 mm

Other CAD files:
body_files/soft_body_construction/cassem.SLDASM
body_files/actuator_mold_construction/flatgroove_rev.SLDASM
sw/last/sg_assem.SLDASM
sw/flatgroove_rev.SLDASM
sw/Assem2.SLDASM
sw/tiltgroove.SLDASM
body_files/actuator_mold_construction/easymodactuator_groove.SLDPRT
body_files/actuator_mold_construction/easymodactuator_groove_rev.SLDPRT
body_files/actuator_mold_construction/grooveblock.SLDPRT
body_files/actuator_mold_construction/grooveblock_rev.SLDPRT
body_files/left_actuator_right.SLDPRT
body_files/right_actuator_right.SLDPRT
body_files/right_acutator_left.SLDPRT
body_files/servo_attachment.SLDPRT
body_files/soft_body_construction/chassis.SLDPRT
prototype_files/solid_chassis_design.SLDPRT
sw/15tall2.5canalL.STL
sw/15tall2.5canalR.STL
sw/15tall7.5canalL.STL
sw/15tall7.5canalR.STL
sw/15tallbar.SLDPRT
sw/15tallbar.STL
sw/30tall2.5canalL.STL
sw/30tall2.5canalR.STL
sw/30tall7.5canalL.STL
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

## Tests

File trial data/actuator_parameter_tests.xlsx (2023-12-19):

Parameters: | Weight |  | Force to bend fully | Weight for free end to bend to 90 |  | Length to bend force | Hole height
Eco 50 7.5 canal 15 tall | 12.5 g |  | ~150g before diminishing | 80 g
Eco 50 2.5 canal 15 tall | 11.5 g |  | ~80g | 30 g
Eco 50 7.5 canal 30 tall | 22.7 g |  | ~60g | 60 g
Eco 50 2.5 canal 30 tall | 20.9 g |  | ~40g | 40 g | <- testing procedure:
Eco 50 5 canal 25 tall | 33.2 g |  | ~70g | 70 g | 1. set actuator against side of table with vertical drop (ensure string doesn't touch edge of table to factor out table friction)
Dragon 30 2.5 canal 15 tall | 11.8 g |  | ~250g | 110 g | 2. add weights on to the hook weight and drop it onto the loop at the end of the actuator
Dragon 30 7.5 canal 15 tall | 12.7 g |  | ~800g | ~450 g | 3. compare bend with bend through finger pulling
Dragon 30 5 canal 25 tall | 35.6 g |  | ~400g | ~400 g | 4. change weights and redrop onto the line to ensure there isnt any retention of shape from the actuator
Dragon 30 2.5 canal 30 tall | 22.5 g |  | ~110g | 110 g | 5. record amount of weight that is close enough to the full finger bend distance before signficant diminishing marginal bend
Dragon 30 7.5 canal 30 tall | 23.7 g |  | ~400g | 400 g
 |  |  |  |  | Less springy from thinner canals
7.5-30 (400) able to flex back |  | dependent on force to flex back
2.5-15 (250) not |  | "angle" of movement very gradually drifts, further testing required
2.5-30 (110) not |  |  | potentially due to different forces, or different lengths of actuators
7.5-15 (800) able
eco 7.5-15 (150) not |  | Movement speed dependent on grooves at bottomside
Later tests: angle of bristles to bend force (against surface)

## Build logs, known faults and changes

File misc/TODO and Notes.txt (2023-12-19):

TODO:
* Design layout for soft body
	* Required components:
		* Two flippers (maybe 3)
		* Two servos (maybe 3)
		* 1 Buck booster
		* 1 dev board
		* 1 battery
		* Wires (negligible)
	* Considerations:
		* IMPORTANT: how to constrain flippers on the soft body?
		* Waterproof? If so, how to design a sealed area for the electronics
			* Would be able to do this ideally, so that the environment is flexible and opens up more potential applications
		* If improving edges does not work, third servo and flipper to push up the body and reduce friction in one direction? Or actuating mass to change friction\
		* Potentially easy way to remove/charge battery
		* The use of a printed board
			* Keeps components in place, can put circles and use "pegs" on the soft body to constrain the electronics

* Add another signal to control the second servo independently
* Print another cap and fix onto the servos

Notes:
* Each mold roughly 30 g for Dragon Skin 30

BUY LIST:
* Servo - https://www.digikey.com/en/products/detail/adafruit-industries-llc/169/5154651
* Boost 3-5V - https://www.digikey.com/en/products/detail/adafruit-industries-llc/4654/12697636
* Resistor kit ?
* New type of cable
	* piano wire other other metal wire
* IR stuff (LEDs, Remote) https://www.digikey.com/en/products/detail/vishay-semiconductor-opto-division/TSOP38238/1681362
* Different types of silicone rubbers
* 90 degree 2pin jst connectors https://www.digikey.com/en/products/detail/jst-sales-america-inc/S2B-PH-K-S-LF-SN/926626
* itsybitsy 3V https://www.digikey.com/en/products/detail/adafruit-industries-llc/3675/8031669
* metro mini 5V https://www.digikey.com/en/products/detail/adafruit-industries-llc/2590/5629422

NOTES FOR THESIS:
* hysteresis-based control (non-linear control)
* wanted to create untethered testbed for said control type
* inspiration from turtle, which can use its flippers to move on land, reset, and repeat

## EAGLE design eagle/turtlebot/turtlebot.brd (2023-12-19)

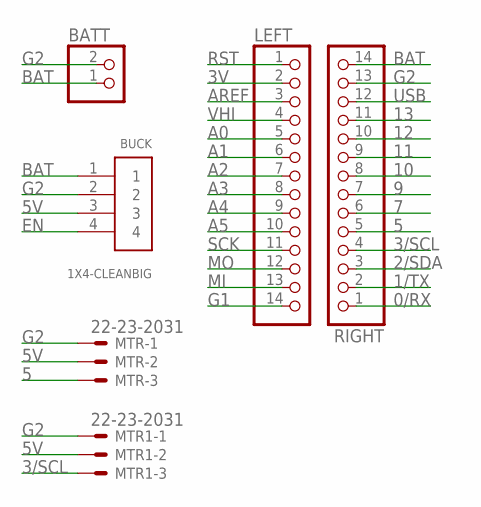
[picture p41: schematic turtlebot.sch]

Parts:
BATT: JST_2PIN-THM-RA; JST-PH-2-THM-RA
BUCK: 1X4-CLEANBIG; 1X04-CLEANBIG
LEFT: MICROBUILDER_HEADER-1X14; MICROBUILDER_1X14_ROUND70
MTR, MTR1: 22-23-2031
RIGHT: MICROBUILDER_HEADER-1X14; MICROBUILDER_1X14_ROUND70

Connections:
0/RX: RIGHT.1
1/TX: RIGHT.2
2/SDA: RIGHT.3
3/SCL: MTR1.3, RIGHT.4
3V: LEFT.2
5: MTR.3, RIGHT.5
5V: BUCK.3, MTR.2, MTR1.2
7: RIGHT.6
9: RIGHT.7
10: RIGHT.8
11: RIGHT.9
12: RIGHT.10
13: RIGHT.11
A0: LEFT.5
A1: LEFT.6
A2: LEFT.7
A3: LEFT.8
A4: LEFT.9
A5: LEFT.10
AREF: LEFT.3
BAT: BATT.1 (2), BUCK.1, RIGHT.14
EN: BUCK.4
G1: LEFT.14
G2: BATT.2 (1), BUCK.2, MTR.1, MTR1.1, RIGHT.13
MI: LEFT.13
MO: LEFT.12
RST: LEFT.1
SCK: LEFT.11
USB: RIGHT.12
VHI: LEFT.4

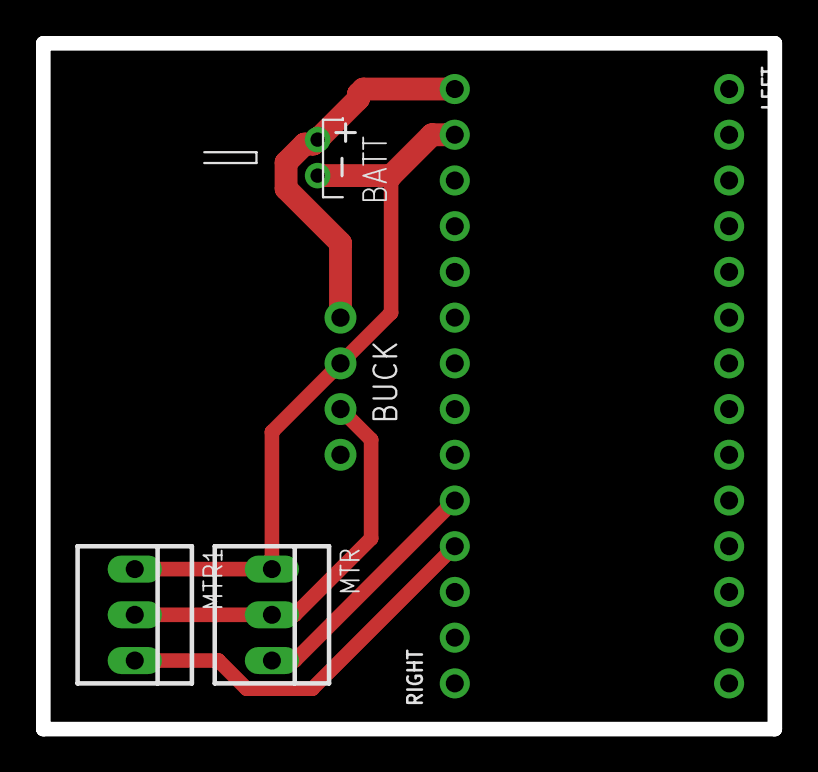
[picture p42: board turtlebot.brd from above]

Board: 2 copper layers, 40.6 x 38.1 mm, 6 parts (0 on the bottom side), 5 nets.

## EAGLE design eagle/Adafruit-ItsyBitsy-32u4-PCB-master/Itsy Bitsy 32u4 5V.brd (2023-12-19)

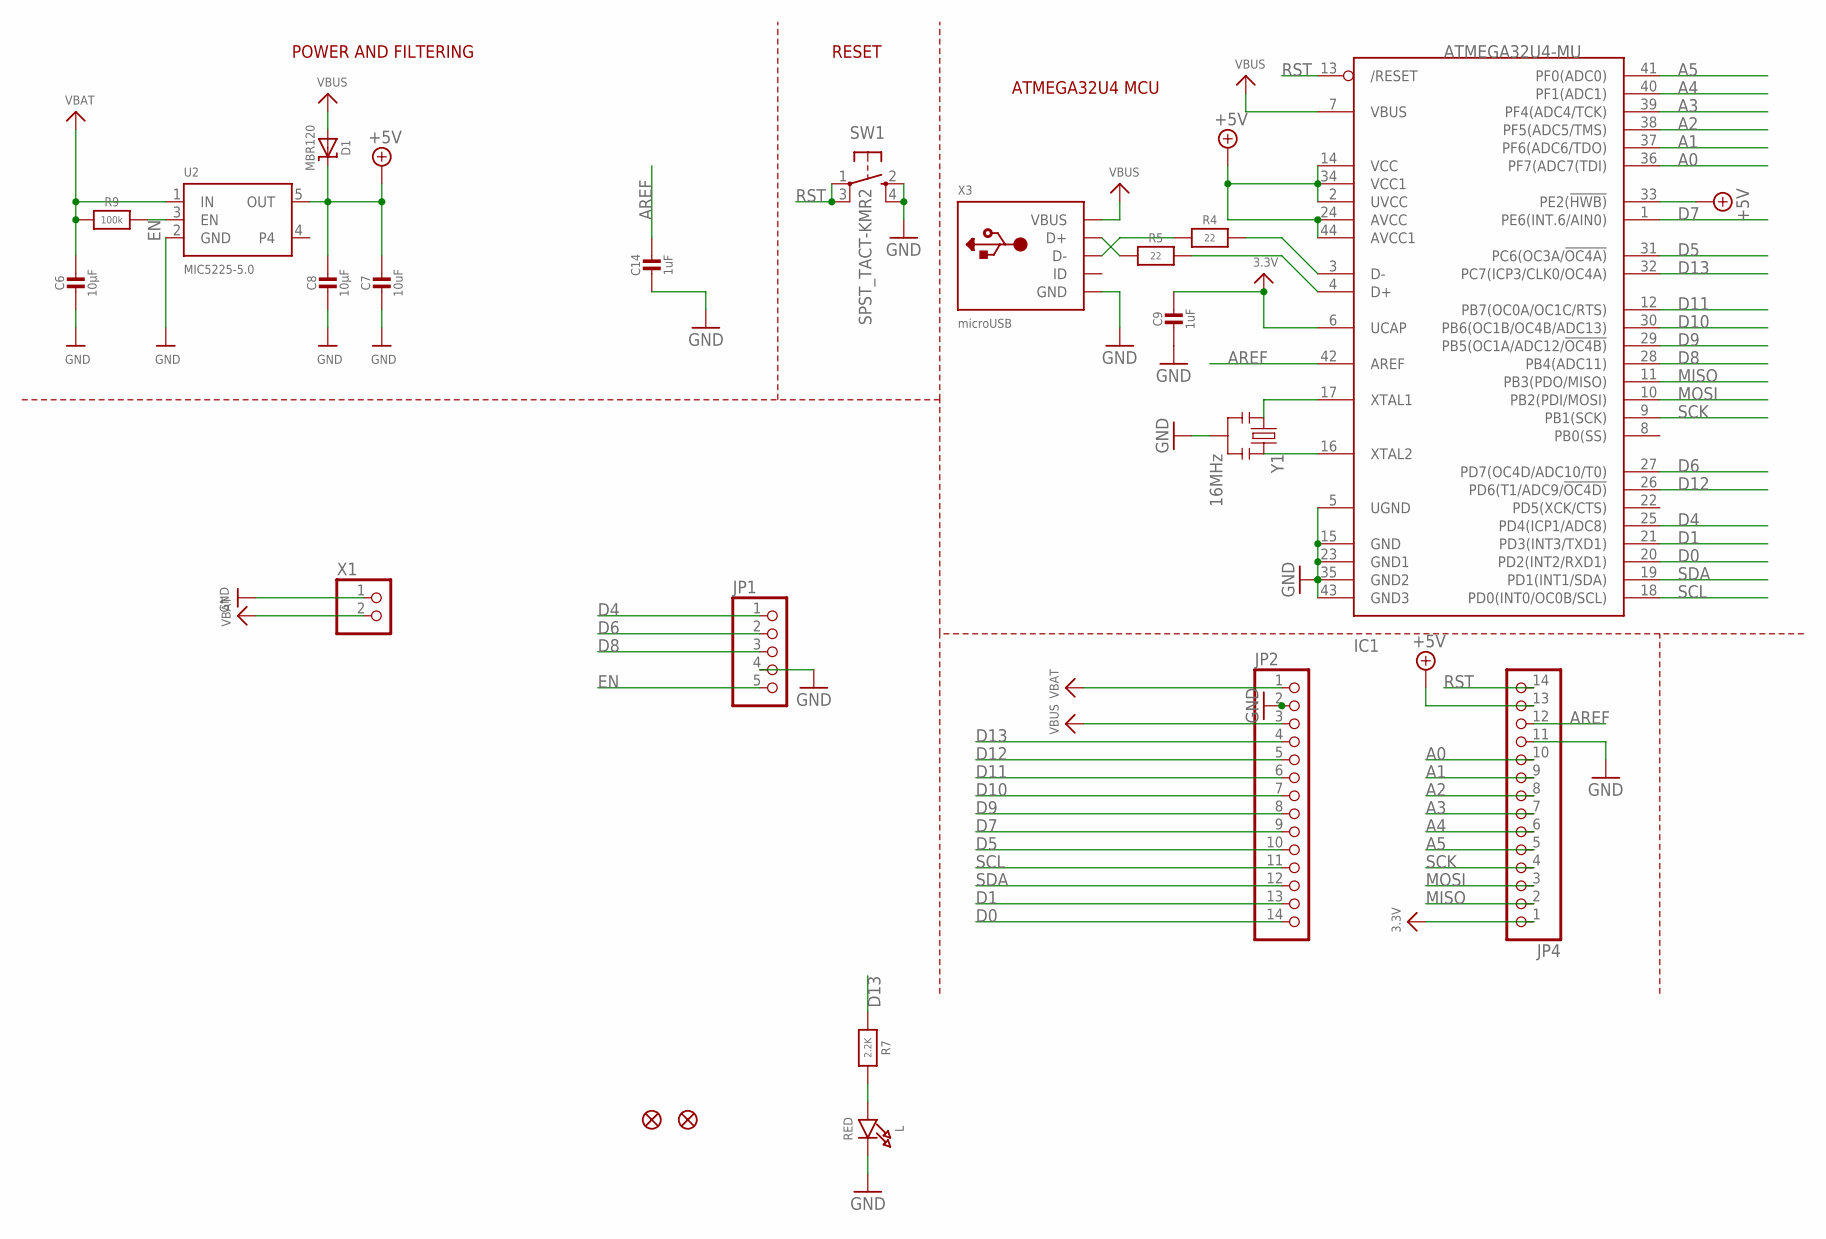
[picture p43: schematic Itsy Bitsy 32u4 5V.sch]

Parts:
C6, C8: 10µF; 0805-NO
C7: 10uF; 0805-NO
C9, C14: 1uF; 0603-NO
D1: MBR120; SOD-123
IC1: ATMEGA32U4-MU; TQFN44_7MM
JP1: HEADER-1X5ROUND; 1X05_ROUND
JP2, JP4: HEADER-1X14; 1X14_ROUND70
L: RED; CHIPLED_0805_NOOUTLINE
R4, R5: 22; 0603-NO
R7: 2.2K; 0603-NO
R9: 100k; 0603-NO
SW1: SPST_TACT-KMR2; KMR2
U2: MIC5225-5.0; SOT23-5
U$34, U$35: FIDUCIAL""; FIDUCIAL_1MM
X1: CON_JST_PH_2PIN; JSTPH2
X3: microUSB; 4UCONN_20329_V2
Y1: 16MHz; RESONATOR-SMD

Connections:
3.3V: C9.1, IC1.6 (UCAP), JP4.1
+5V: C7.1, C8.1, D1.C, IC1.2 (UVCC), IC1.14 (VCC), IC1.24 (AVCC), IC1.33 (PE2(!HWB)), IC1.34 (VCC1), IC1.44 (AVCC1), JP4.13, U2.5 (OUT)
A0: IC1.36 (PF7(ADC7(TDI)), JP4.10
A1: IC1.37 (PF6(ADC6/TDO)), JP4.9
A2: IC1.38 (PF5(ADC5/TMS)), JP4.8
A3: IC1.39 (PF4(ADC4/TCK)), JP4.7
A4: IC1.40 (PF1(ADC1)), JP4.6
A5: IC1.41 (PF0(ADC0)), JP4.5
AREF: C14.1, IC1.42 (AREF), JP4.12
D0: IC1.20 (PD2(INT2/RXD1)), JP2.14
D1: IC1.21 (PD3(INT3/TXD1)), JP2.13
D4: IC1.25 (PD4(ICP1/ADC8)), JP1.1
D5: IC1.31 (PC6(OC3A/!OC4A)), JP2.10
D6: IC1.27 (PD7(OC4D/ADC10/T0)), JP1.2
D7: IC1.1 (PE6(INT.6/AIN0)), JP2.9
D8: IC1.28 (PB4(ADC11)), JP1.3
D9: IC1.29 (PB5(OC1A/ADC12/!OC4B)), JP2.8
D10: IC1.30 (PB6(OC1B/OC4B/ADC13)), JP2.7
D11: IC1.12 (PB7(OC0A/OC1C/RTS)), JP2.6
D12: IC1.26 (PD6(T1/ADC9/!OC4D)), JP2.5
D13: IC1.32 (PC7(ICP3/CLK0/OC4A)), JP2.4, R7.1
D+: IC1.4 (D+), R5.2
D-: IC1.3 (D-), R4.2
EN: JP1.5, R9.2, U2.3 (EN)
GND: C6.2, C7.2, C8.2, C9.2, C14.2, IC1.5 (UGND), IC1.15 (GND), IC1.23 (GND1), IC1.35 (GND2), IC1.43 (GND3), JP1.4, JP2.2, JP4.11, L.C, SW1.2 (S), SW1.4 (S1), U2.2 (GND), X1.1, X3.BASE@1 (GND), X3.BASE@2 (GND), X3.GND, X3.SPRT@1 (GND), X3.SPRT@2 (GND), X3.SPRT@3 (GND), X3.SPRT@4 (GND), Y1.2
MISO: IC1.11 (PB3(PDO/MISO)), JP4.2
MOSI: IC1.10 (PB2(PDI/MOSI)), JP4.3
unnamed: L.A, R7.2
unnamed: IC1.16 (XTAL2), Y1.3
unnamed: IC1.17 (XTAL1), Y1.1
unnamed: R5.1, X3.D+
unnamed: R4.1, X3.D-
RST: IC1.13 (/RESET), JP4.14, SW1.1, SW1.3 (P1)
SCK: IC1.9 (PB1(SCK)), JP4.4
SCL: IC1.18 (PD0(INT0/OC0B/SCL)), JP2.11
SDA: IC1.19 (PD1(INT1/SDA)), JP2.12
VBAT: C6.1, JP2.1, R9.1, U2.1 (IN), X1.2
VBUS: D1.A, IC1.7 (VBUS), JP2.3, X3.VBUS

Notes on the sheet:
POWER AND FILTERING
RESET
ATMEGA32U4 MCU

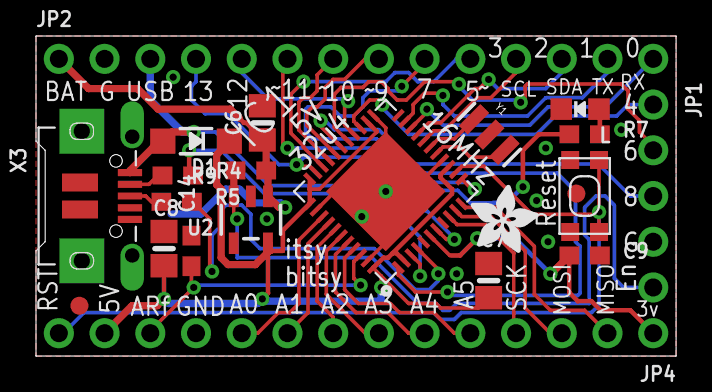
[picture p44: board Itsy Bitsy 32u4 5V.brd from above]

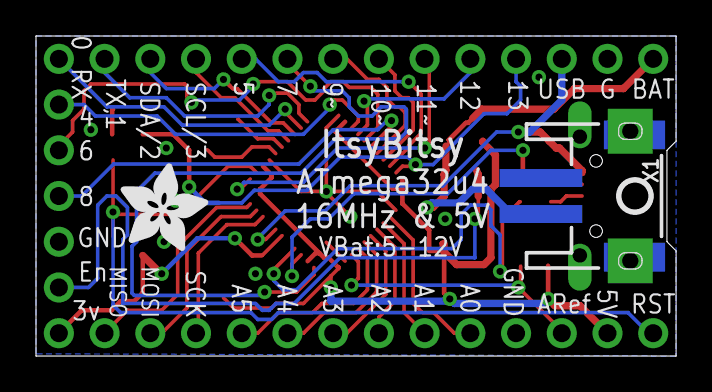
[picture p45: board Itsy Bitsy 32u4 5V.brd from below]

Board: 2 copper layers, 35.6 x 17.8 mm, 25 parts (3 on the bottom side), 38 nets.

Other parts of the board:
U$4: ADAFRUIT_5MM
U$7: ADAFRUIT_3.5MM
U$10: PCBFEAT-REV-040

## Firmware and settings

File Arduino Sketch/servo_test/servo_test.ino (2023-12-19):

#include <Servo.h>

Servo s1;
Servo s2;
int servo1_pin = 3;
int servo2_pin = 5;
int pos1 = 0;
int pos2 = 0;

int pmin = 5;
int pmax = 90;

void setup() {
  s1.attach(servo1_pin);
  s2.attach(servo2_pin);
  // s1.write(90);
}

void loop() {
  if (s1.read() != pmin || s2.read() != pmin) {
    for (pos1 = s1.read(); pos1 >= pmin; pos1 -= 5) {
      s1.write(pos1);
      s2.write(pos1);
      delay(15);
    }
    delay(500);
  }
  // if (s2.read() != pmin) {
  //   for (pos2 = s2.read(); pos2 >= pmin; pos2 -= 5) {
  //     s2.write(pos2);
  //     delay(15);
  //   }
  //   delay(500);
  // }
  
  for (pos1 = pmin; pos1 <= pmax; pos1 += 5) { // goes from 0 degrees to 180 degrees
    // in steps of 1 degree
    s1.write(pos1);              // tell servo to go to position in variable 'pos'
    s2.write(pos1);
    delay(15); // delay to allow the servo to reach the desired position
    // if (pos==90){
    //   delay(1000); //wait 5 seconds once positioned at 90 degrees
    // }
  }
  delay(500); // wait 5 seconds after reaching 180 degrees
 
  for (pos1 = pmax; pos1 >= pmin; pos1 -= 5) { // goes from 180 degrees to 0 degrees
    s1.write(pos1);              // tell servo to go to position in variable 'pos'
    s2.write(pos1);
    delay(15);
    // if (pos==90){
    //   delay(1000); // wait 5 seconds once positioned at 90 degrees
    // }
  }
  delay(500); // wait 5 seconds after arriving back at 0 degrees
}

// void setup() {

// }

// void loop() {

// }

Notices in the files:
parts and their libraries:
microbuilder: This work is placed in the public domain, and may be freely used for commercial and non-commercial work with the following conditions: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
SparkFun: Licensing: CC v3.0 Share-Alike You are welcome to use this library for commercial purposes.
